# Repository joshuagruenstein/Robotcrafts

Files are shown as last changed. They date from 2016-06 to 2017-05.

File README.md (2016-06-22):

# Robotcrafts



Robotcrafts (working title) is a low cost "arts &amp; crafts" style kit for remote control robots.  The first prototype was created in the summer of 2015 for a robotics elective at [Camp Good Grief](https://www.eeh.org/bereavement/camp-good-grief/) at [East End Hospice](https://www.eeh.org/) in Southold, NY.  This repository covers all future versions of this concept, from 2016 onwards.

## Concept

The kit is comprised of a controller, motors, wheels, and standard arts &amp; crafts materials such as foamcore, double sided tape, and popsicle sticks.  The controller is a dual layer PCB with four pushbuttons, three AA batteries, and copper pads to attach the motor wires via alligator clips.   The motors are given to the children with 5ft of twisted leads attached to them, terminated with alligator clips.  All the kids have to do is clip the alligator clips onto the controller, allowing them to use the buttons to move the motors forwards and backwards.  

This design gives kids the freedom to experiment with different robot designs using existing arts and crafts skills, as it removes the challenge of wiring up a robot.  However, the electronics are still both simple enough to understand and cheap enough to give a robot per child: the goal is to price each kit at ~$10.  While this may not be economically feasible for every application, it's obviously still ideal to get kits such as these in the hands of as many kids as possible.

## Implementation

The current implementation uses a Toshiba TB6612FNG dual brushed motor controller and Dagu gearmotors and wheels.  The controller PCB is in EagleCAD, which while not being free software seems to be the standard over KiCAD for hobbyists, making it more "open" to the community.  These parts were chosen for their low price at the required scale.

An issue with the current implementation is ease of manufacturing: the process of soldering leads to the motors, applying hot glue for strain relief, attaching alligator clips, and soldering DIP and SMD parts to the PCB is quite laborious, especially in large quantities.  Last summer I spent a full day assembling ~25 kits of lesser complexity.  I'm not quite sure what to do about this at the moment except to allot more time for assembly, so if you have an idea please submit an issue or pull request.

## Photos

Below are some fun pictures of some of the robots kids at Camp Good Grief made last summer:

Robot Picture with Controller

Heart Robot Picture

Kitty Robot Picture

Popsicle Robot Picture

## Contributing

Please feel free to contribute, whether it be to suggest a feature or design change, update a schematic, or add pictures of a robot you've made!  Just submit either an issue or a pull request.



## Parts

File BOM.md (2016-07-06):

#Bill of Materials

Below is a work in progress bill of materials for each individual kit.  This only includes "robot parts," and does not include (necessary) building supplies such as double sided tape and foam-core/cardboard.  This also leaves out "bulk products" such as 22awg wire, which can be purchased most economically by the roll.  Part pricing is assuming 25x kit production.

| Quantity | Description | Vendor | Product # | Price | Total  |
|---|---|---|---|---|---|
| 1 | Hobby Gearmotor Pair | Sparkfun | ROB-13258 | $3.95 | $3.95  |
| 1 | 65mm Wheel Pair | Sparkfun | ROB-13259 | $2.95 | $2.95  |
| 1 | TB6612FNG Dual Motor Driver | Digikey  | TB6612FNGC8ELCT-ND  | $1.42 | $1.42  |
| 4 | 12mm Pushbutton Switch | Digikey  | 450-1157-ND | $0.27 | $1.07  |
| 4 | 10k 0805 Resistor | Digikey  | RMCF0805JT10K0CT-ND | $0.01 | $0.03  |
| 6 | AA Battery Clip | Digikey  | 36-92-ND | $0.22 | $1.33  |
| 4 | Alligator Clip | Digikey  | 290-1951-ND | $0.17 | $0.66  |
| | | | | **Kit Sum:** | $11.40 |

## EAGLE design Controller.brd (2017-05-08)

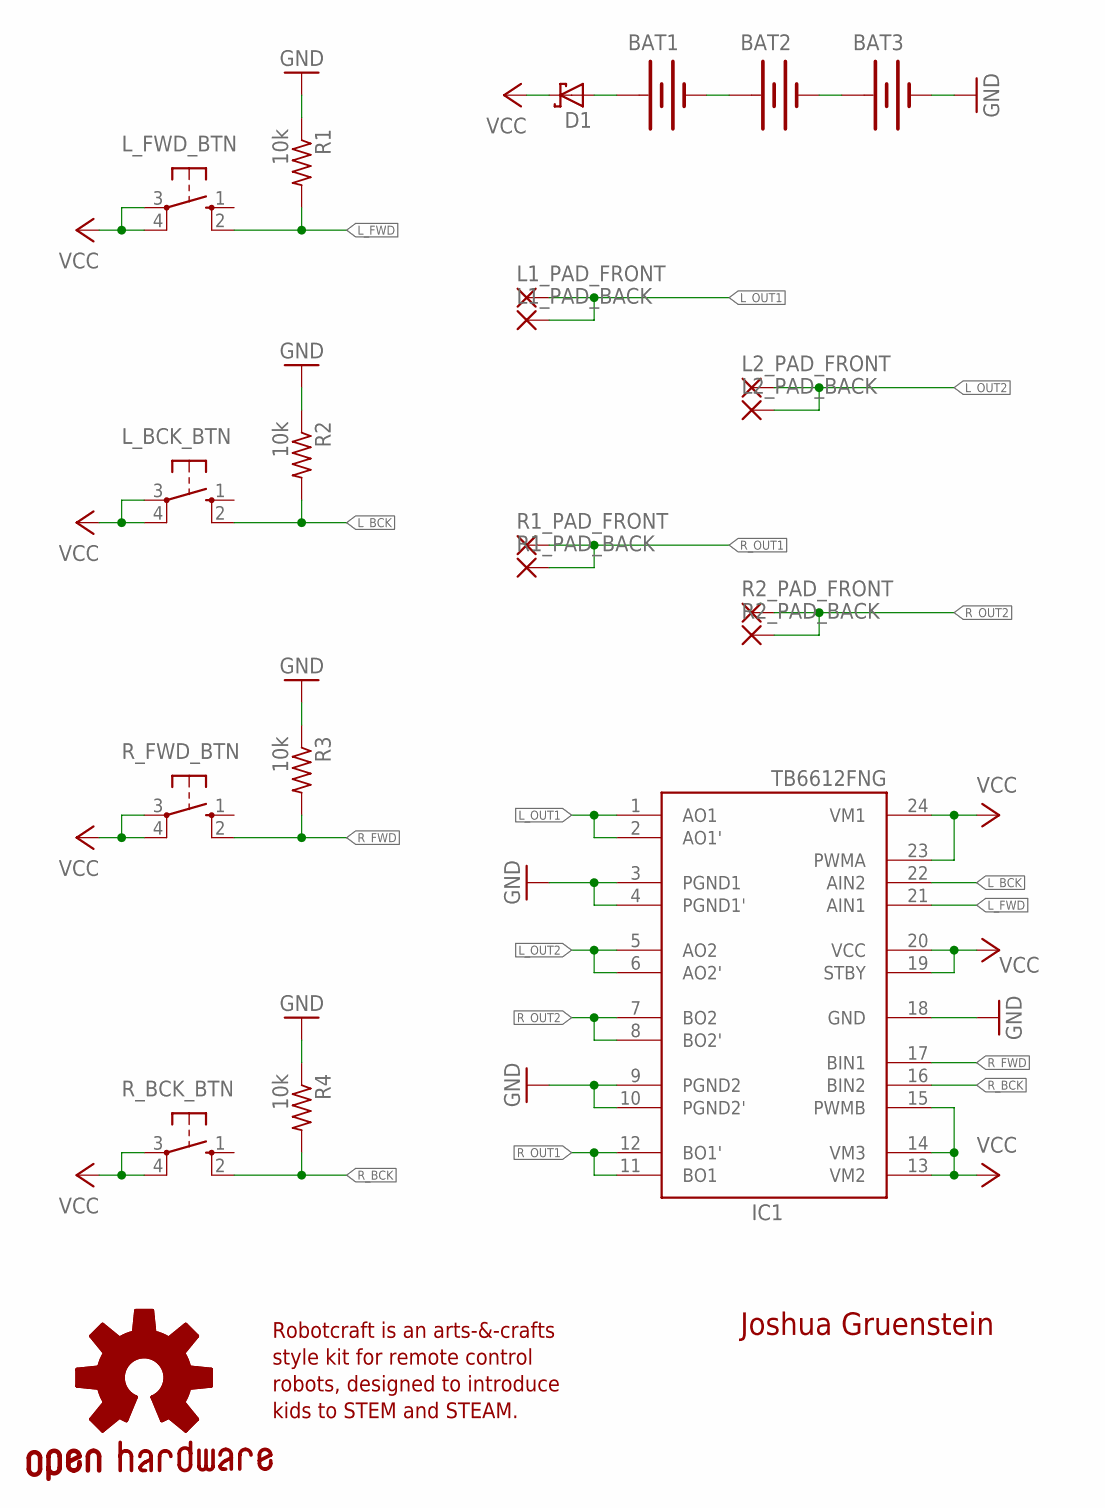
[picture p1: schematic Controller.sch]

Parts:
BAT1, BAT2, BAT3: BATTERYAA-KIT; BATTERY-AA-KIT
D1: SCHOTTKY-DIODESMC; SMC
GOLD_ORB_SM1: OSHWLOGO_GOLD_ORB_MED; OSHW1
IC1: TB6612FNG; SSOP24
L1_PAD_BACK, L1_PAD_FRONT, L2_PAD_BACK, L2_PAD_FRONT: WIREPADSMD5-2,5; 5-2,5
L_BCK_BTN: 40-XX; B3F-40XX
L_FWD_BTN: 40-XX; B3F-40XX
R1, R2, R3, R4: 10k; R0805
R1_PAD_BACK, R1_PAD_FRONT, R2_PAD_BACK, R2_PAD_FRONT: WIREPADSMD5-2,5; 5-2,5
R_BCK_BTN: 40-XX; B3F-40XX
R_FWD_BTN: 40-XX; B3F-40XX

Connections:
GND: BAT3.GND@1 (-), IC1.3 (PGND1), IC1.4 (PGND1'), IC1.9 (PGND2), IC1.10 (PGND2'), IC1.18 (GND), R1.1, R2.1, R3.1, R4.1
L_BCK: IC1.22 (AIN2), L_BCK_BTN.2 (S1), R2.2
L_FWD: IC1.21 (AIN1), L_FWD_BTN.2 (S1), R1.2
L_OUT1: IC1.1 (AO1), IC1.2 (AO1'), L1_PAD_BACK.1, L1_PAD_FRONT.1
L_OUT2: IC1.5 (AO2), IC1.6 (AO2'), L2_PAD_BACK.1, L2_PAD_FRONT.1
unnamed: BAT1.GND@1 (-), BAT2.PWR@1 (+)
unnamed: BAT2.GND@1 (-), BAT3.PWR@1 (+)
unnamed: BAT1.PWR@1 (+), D1.A
R_BCK: IC1.16 (BIN2), R4.2, R_BCK_BTN.2 (S1)
R_FWD: IC1.17 (BIN1), R3.2, R_FWD_BTN.2 (S1)
R_OUT1: IC1.11 (BO1), IC1.12 (BO1'), R1_PAD_BACK.1, R1_PAD_FRONT.1
R_OUT2: IC1.7 (BO2), IC1.8 (BO2'), R2_PAD_BACK.1, R2_PAD_FRONT.1
VCC: D1.C, IC1.13 (VM2), IC1.14 (VM3), IC1.15 (PWMB), IC1.19 (STBY), IC1.20 (VCC), IC1.23 (PWMA), IC1.24 (VM1), L_BCK_BTN.3, L_BCK_BTN.4 (P1), L_FWD_BTN.3, L_FWD_BTN.4 (P1), R_BCK_BTN.3, R_BCK_BTN.4 (P1), R_FWD_BTN.3, R_FWD_BTN.4 (P1)

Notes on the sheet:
Joshua Gruenstein
Robotcraft is an arts-&-crafts style kit for remote control robots, designed to introduce kids to STEM and STEAM.

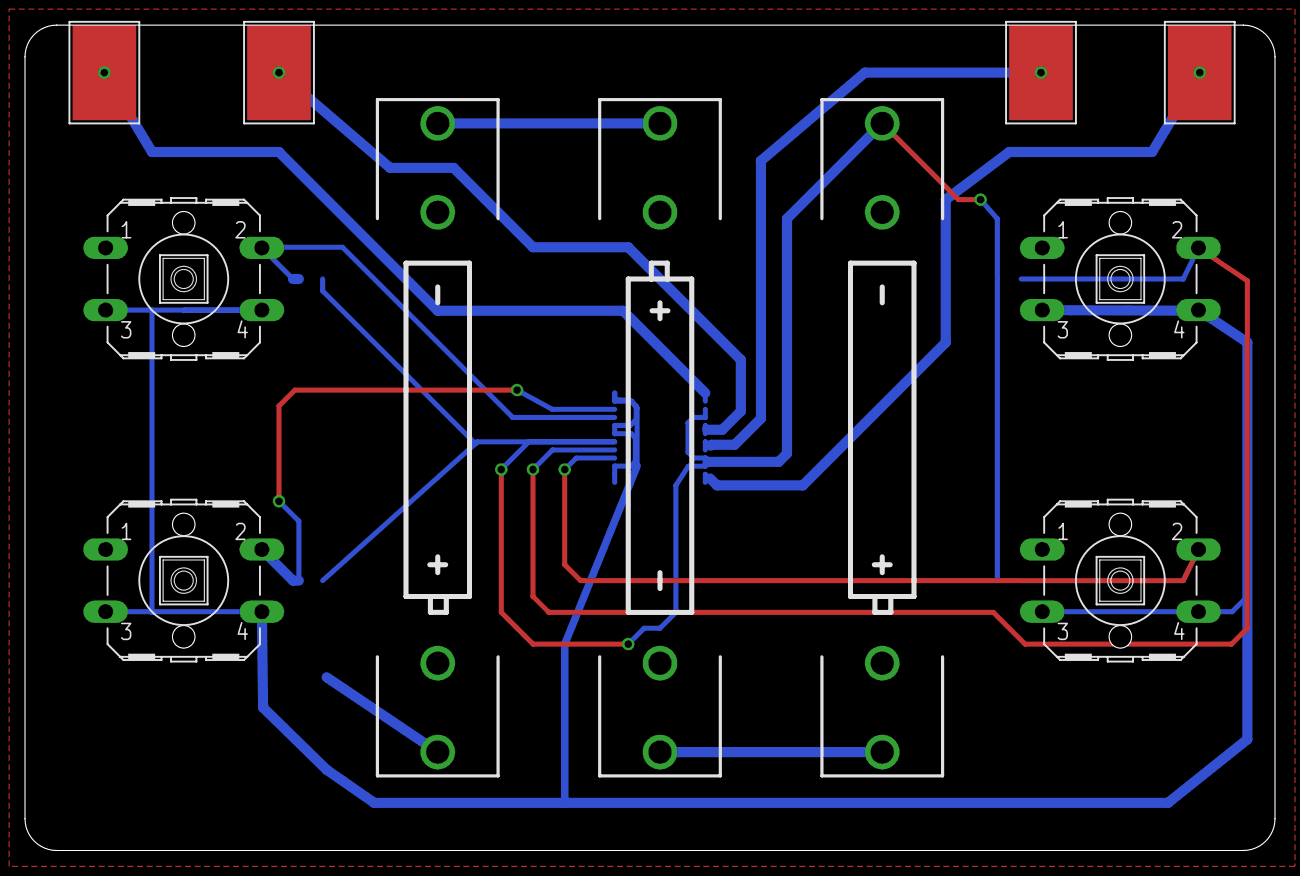
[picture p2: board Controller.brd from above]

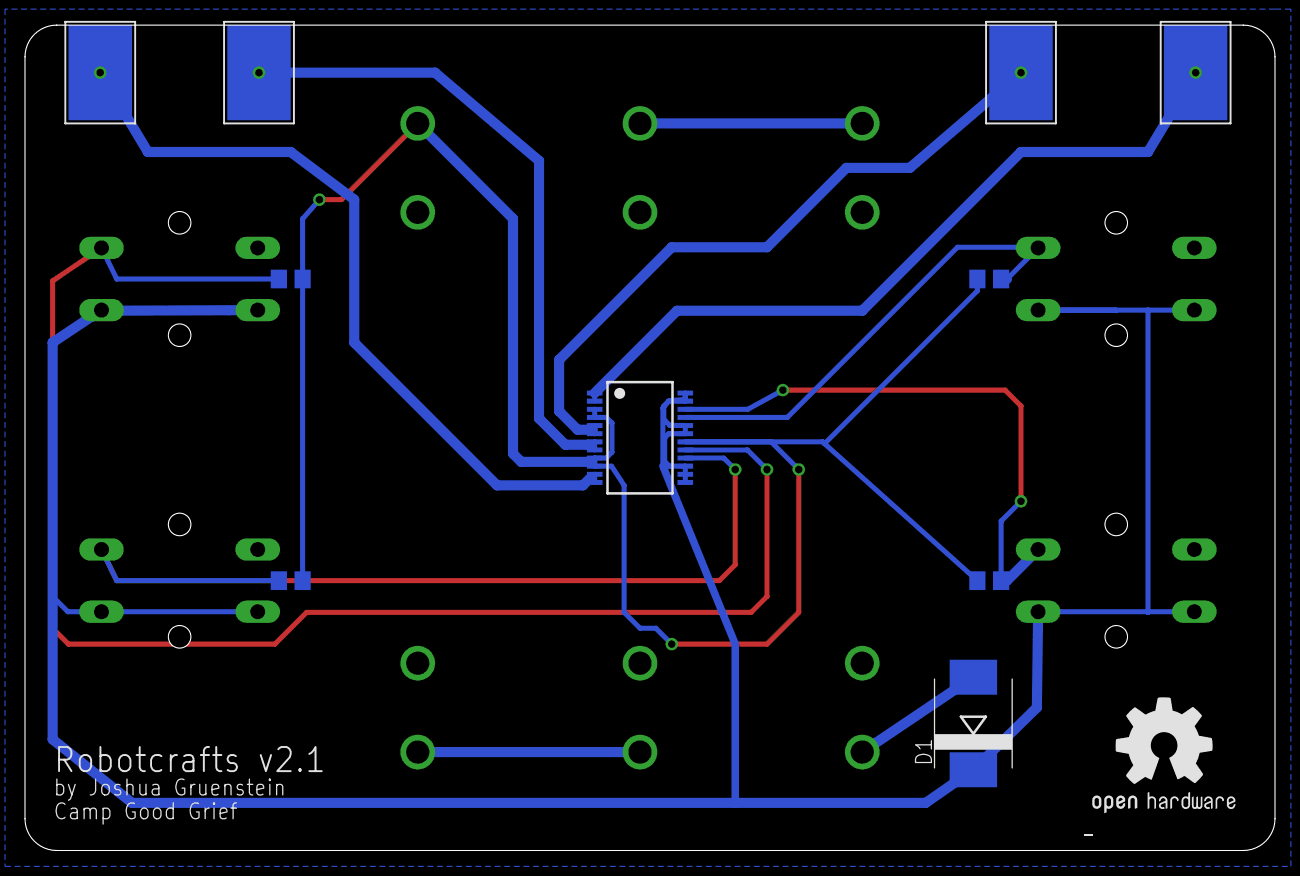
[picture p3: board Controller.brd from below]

Board: 2 copper layers, 100.0 x 66.0 mm, 22 parts (11 on the bottom side), 13 nets.

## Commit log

2016-06-22 add bill of materials
2016-06-22 initial controller schematic
    [Controller.sch]
2016-06-27 add motor pads
    [Controller.sch]
2016-06-27 add fancy A5 portrait frame to schematic
    [Controller.sch]
2016-06-27 initial board component layout
    [Controller.brd]
2016-07-06 initial board routing
    [Controller.brd]
2016-07-06 add ground copper fills
    [Controller.brd]
2016-07-06 board version + author silkscreen
    [Controller.brd]
2016-07-06 v0.1 gerber files
    [Controller.GBL, Controller.GBO, Controller.GBS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]
2016-07-06 adjust silkscreen
    [Controller.brd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]
2016-07-06 update BOM
2016-07-12 pcb rounded corners
    [Controller.brd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]
2016-07-14 cosmetic PCB upgrades
    added OSHW logo to bottom silkscreen
    [Controller.brd, Controller.sch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]
2016-07-14 enlarge board alligator pad size
    [Controller.brd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]
2016-07-22 fix button alignment
    in other news, I got the 0.2 PCBs back today and they are **gorgeous**
    [Controller.brd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]
2016-07-28 update silkscreen to v2.0
    [Controller.brd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]
2017-05-08 add diode to board and schematic
    [Controller.brd, Controller.sch]

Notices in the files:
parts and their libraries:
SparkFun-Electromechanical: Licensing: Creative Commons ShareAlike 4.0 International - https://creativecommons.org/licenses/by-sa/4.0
